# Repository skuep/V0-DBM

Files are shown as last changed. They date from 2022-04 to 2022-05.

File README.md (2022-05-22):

# V0-DBM
This is a high-resolution *differential pulley system* belt mod for the Z-axis on Voron 0 with optional Kirigami Bed support. There are quite a lot of belt mods out there, but this one differs significantly in how the mechanical advantage is implemented to achieve the same (or better) gearing ratio (notice the lack of an 80T pulley).

NOTE: This is an alpha version and heavy work in progress! Things are mostly tested and working, however there WILL be road bumps ahead and a Voron-style instruction manual is not available. Use the interactive 3D Model on Onshape below for assembly help. Please read this README carefully and in its entirety.

[See at Onshape](https://cad.onshape.com/documents/652155fb16d5bfa4e40363ce/w/0de7fce5d378ec45beba7939/e/0d8c25df57177126b288434d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) | [Demonstration Video](https://www.reddit.com/r/VORONDesign/comments/txs1nn/what_do_you_guys_think_of_a_differential_pulley/?sort=new)

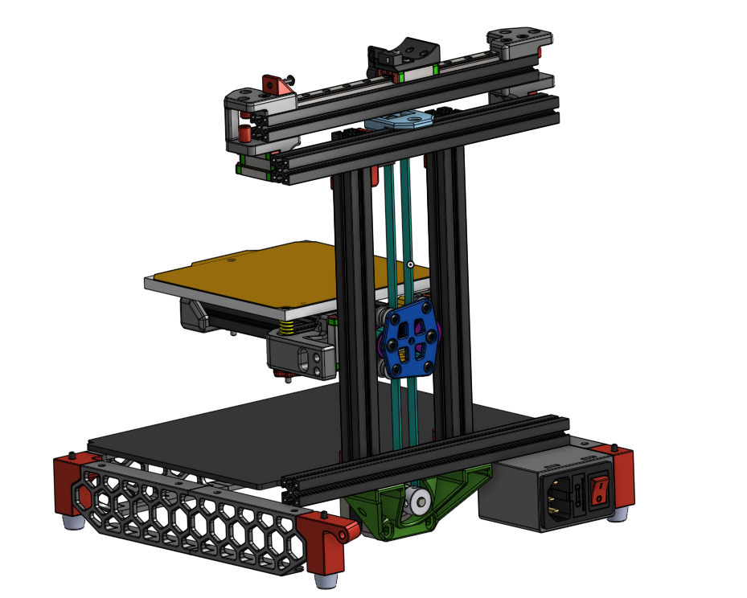
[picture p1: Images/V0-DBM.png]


## What?
A differential pulley system! It is a long known pulley system for achieving extremely high mechanical advantage using just pulleys and a belt.
See the [Wikpedia](https://en.wikipedia.org/wiki/Differential_pulley) article for more information on how this pulley system works. In this case, I split up the central shaft (connecting the two unequal pulleys) into two shafts and connected them with a small belt. This way we eliminate the belt crossing.

## Why?
I wanted a V0 Belt mod, that eliminates the 80T pulley for stepping down the motion and increasing torque that is used in all other belt mods. Also achieving relatively high mechanical advantage is no problem for differential pulley systems. In the differential pulley system, the "gear ratio" is integrated in the belt system. In this case, the two double pulleys have a combined teeth ratio of 27/33. Taking the Wikipedia article as a base, the following formula was derived to calculate the mechanical advantage in this system:

MA = 2/(1-r/R)-1 = 2/(1-27/33)-1 = 10

With the 20T motor pulley (2mm pitch, i.e. 40mm per revolution), this achieves a 40mm/10=4mm per revolution Z-axis advance or 0.01mm per stepper half-step with a regular 1.8° stepper motor.

Also the mechanism looks cool and is underrated. When you press me hard to find an advantage of this mod, I think this mod has less (special) parts than other belt mods.

NOTE: Theoretically gear ratios of 16 or 32 are possible with combined pulley ratios of 30/34 or 31/33, respectively. With a 16T pulley this allows a resolution of 2mm or even 1mm per revolution.

## Note on Kirigami Bed
For the Kirigami bed, you need to drill two extra 3mm holes for the two screws acting as the two shafts. Print and mount the drill-guide from the STLs to your Kirigami bed and drill in the designated holes with a 3mm drill bit. If your bed is made from Aluminium, you can deburr the drill-exit wound with a sharp exacto-knife.

## BOM
You need the following extra parts (this list is probably incomplete):
- 20T pulley for stepper motor
- 20T toothed idler (with bearing ID 3mm)
- 2x M3x40 BHCS (M3x30 BHCS with Kirigami Bed)
- 5x M3x16 BHCS
- 3x M3x6 BHCS
- 4x M3x8 BHCS
- 22x 0.5mm shim washer
- A bunch of heat-stake inserts
- 2GT belt 112mm (110mm also possible when changing to 27/26 and 26/33 pulleys, contact me in this case)
- 2GT belt 500mm

## ToDo
This repository is highly work in progress, the following things are still not satisfying:
- The endstop is actuated by the flange of one of the F623 bearings. Not nice but works for now.
- Documentation/Images on how to assemble

Feel free to use, open issues or leave alone :-)

## Known Issues
Unfortunately I could not get a very linear motion out of this system yet. I recorded Z movement with a dial test indicator in 0.1mm increments and the accuracy is only around +/-50 um (worst case). I think this is not enough and is probably due to the belt, that "pulls" the bed up being fed through multiple (3d printed) pulleys. In fact, both small pulleys and the belt-length can be found as a periodicity in the Z position error (even with original Gates belts). That is why I currently do not recommend this mechanism for the Z-axis drive.

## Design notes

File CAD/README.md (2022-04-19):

# Please download most current CAD data from the Onshape project

https://cad.onshape.com/documents/652155fb16d5bfa4e40363ce/w/0de7fce5d378ec45beba7939/e/0d8c25df57177126b288434d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

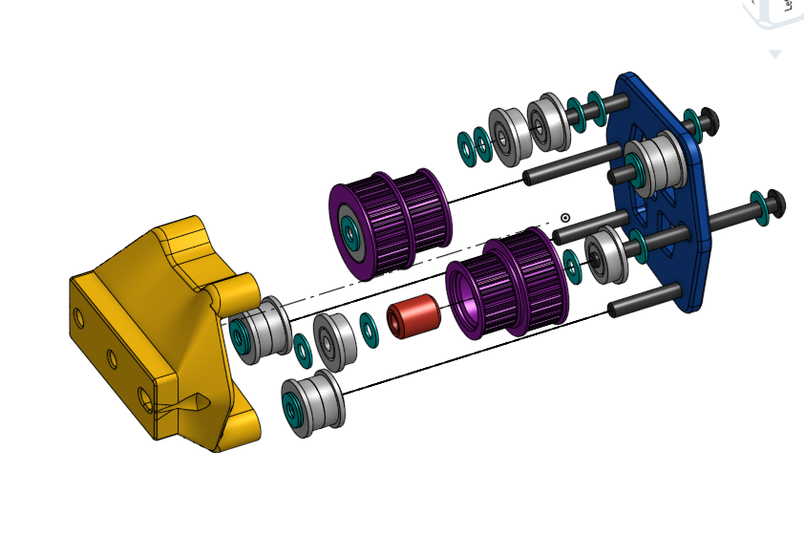
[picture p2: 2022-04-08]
Images/pulley-exploded.png

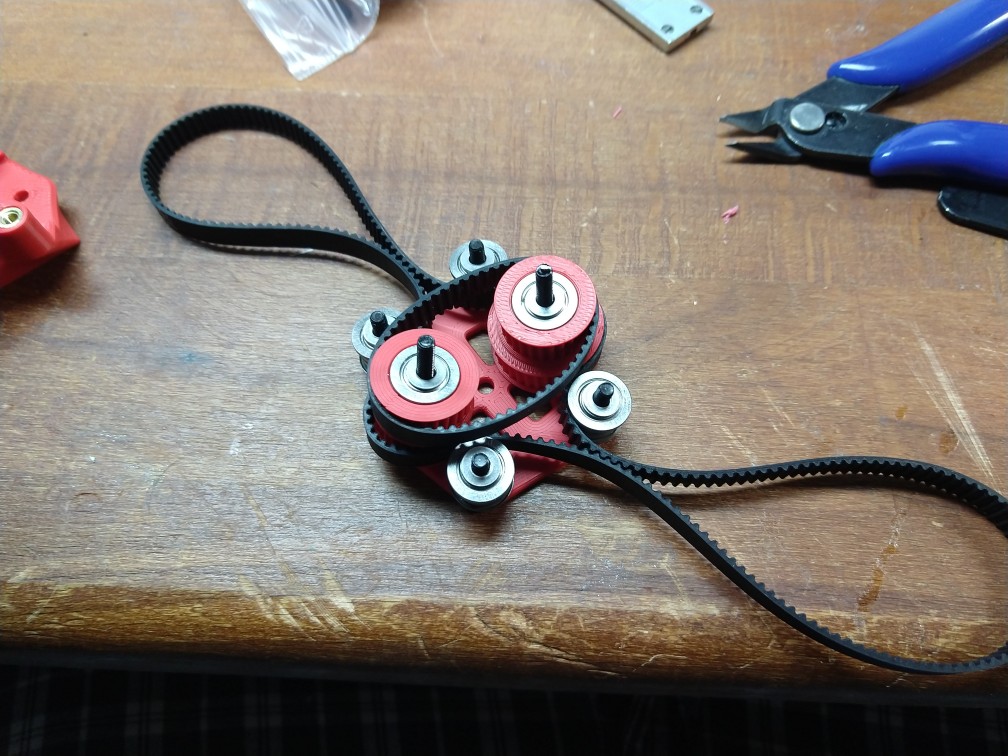
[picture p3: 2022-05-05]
Photos/Pulley-Assy.jpg

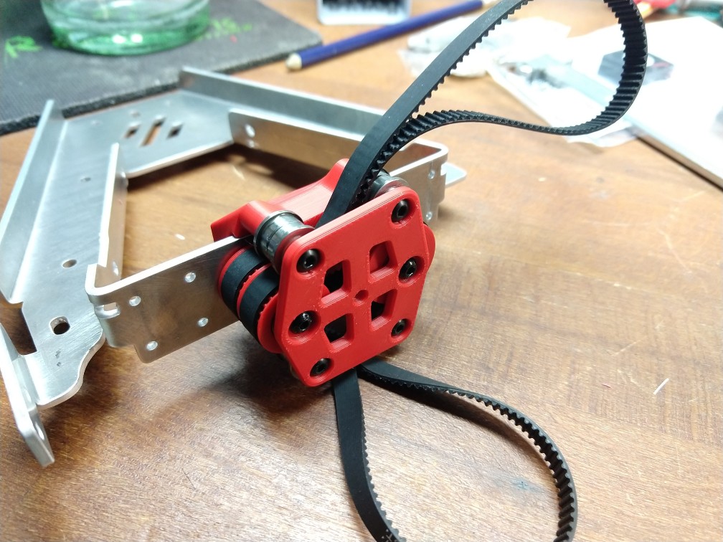
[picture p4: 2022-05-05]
Photos/Bedmount-Kirigami.jpg

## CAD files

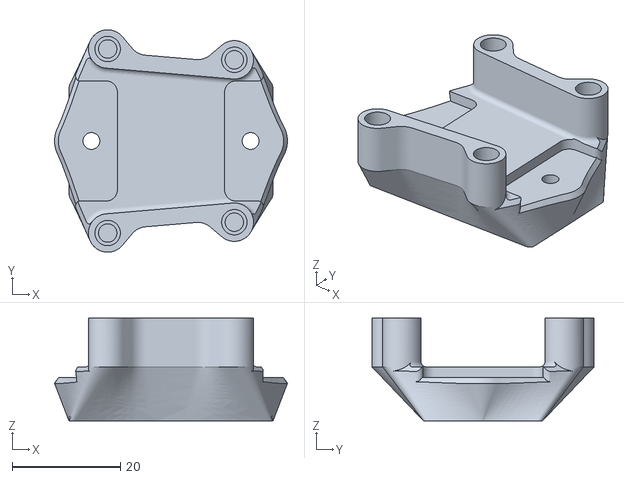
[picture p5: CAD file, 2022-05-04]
STL/Bedmount-Kirigami.stl
43.0 x 41.1 x 19.0

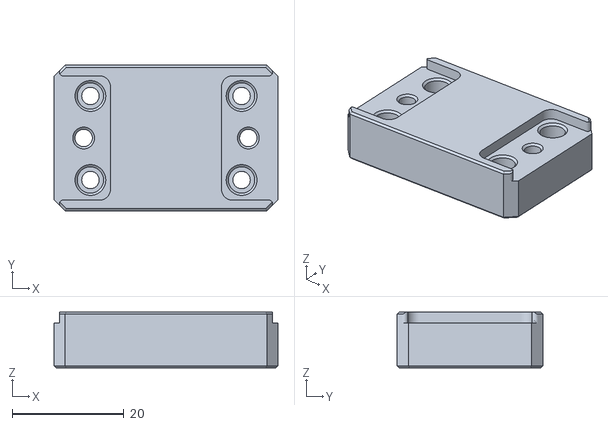
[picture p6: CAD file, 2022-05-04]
STL/Kirigami-Drillguide.stl
40.0 x 26.0 x 10.0

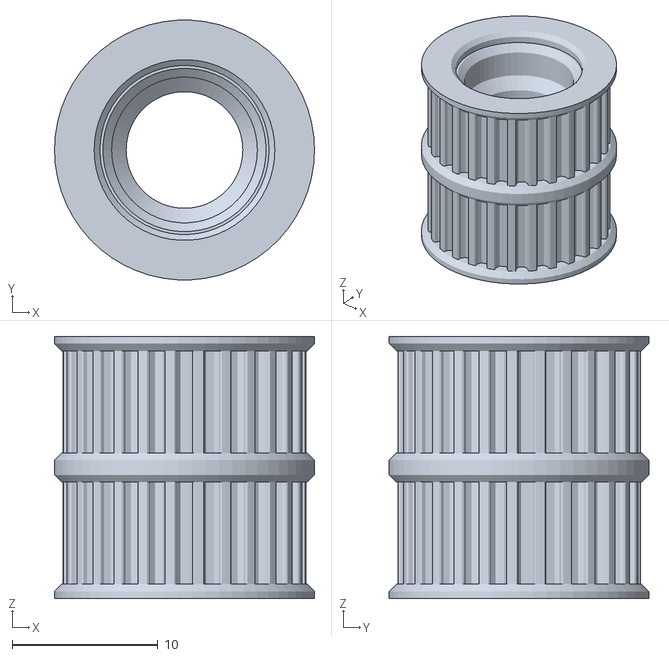
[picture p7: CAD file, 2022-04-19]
STL/Double-Pulley-27-27.stl
17.8 x 17.8 x 18.0

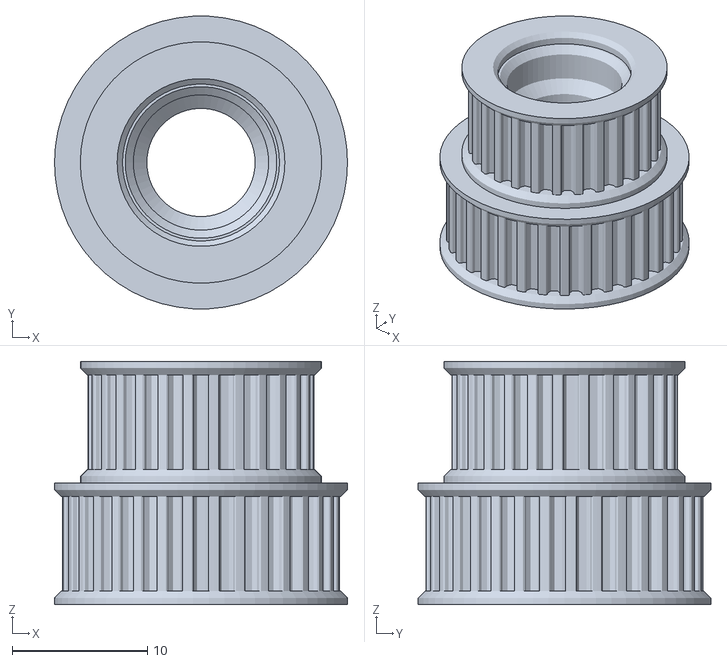
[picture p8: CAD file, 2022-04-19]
STL/Double-Pulley-27-33.stl
21.7 x 21.6 x 18.0

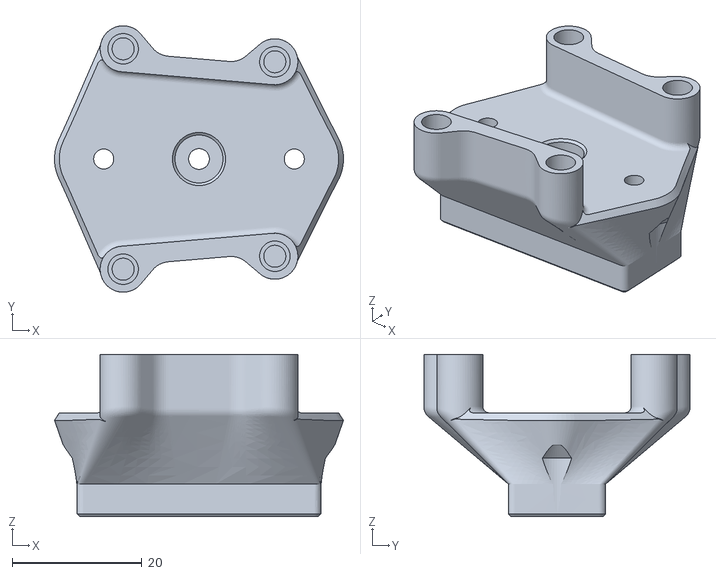
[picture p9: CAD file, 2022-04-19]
STL/Bedmount-Standard.stl
44.6 x 41.1 x 25.0

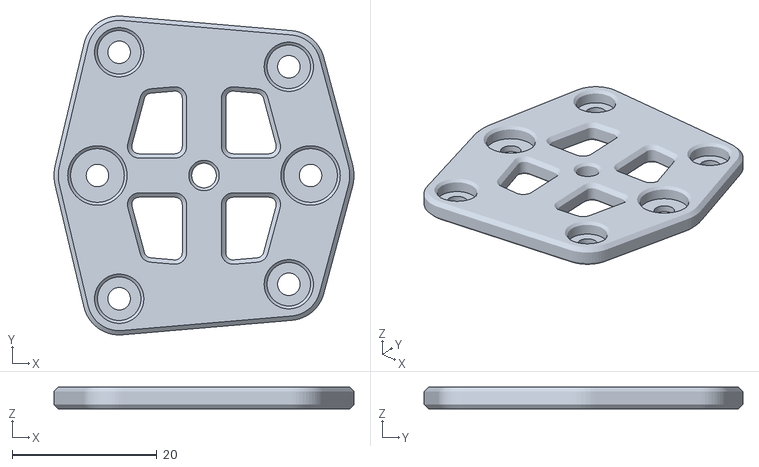
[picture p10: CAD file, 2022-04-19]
STL/Brace.stl
41.4 x 44.0 x 3.00

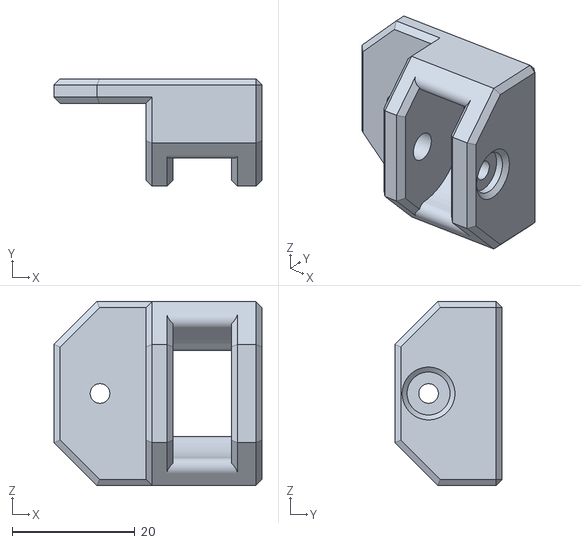
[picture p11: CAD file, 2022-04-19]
STL/Idler-Bracket.stl
33.9 x 17.5 x 30.0

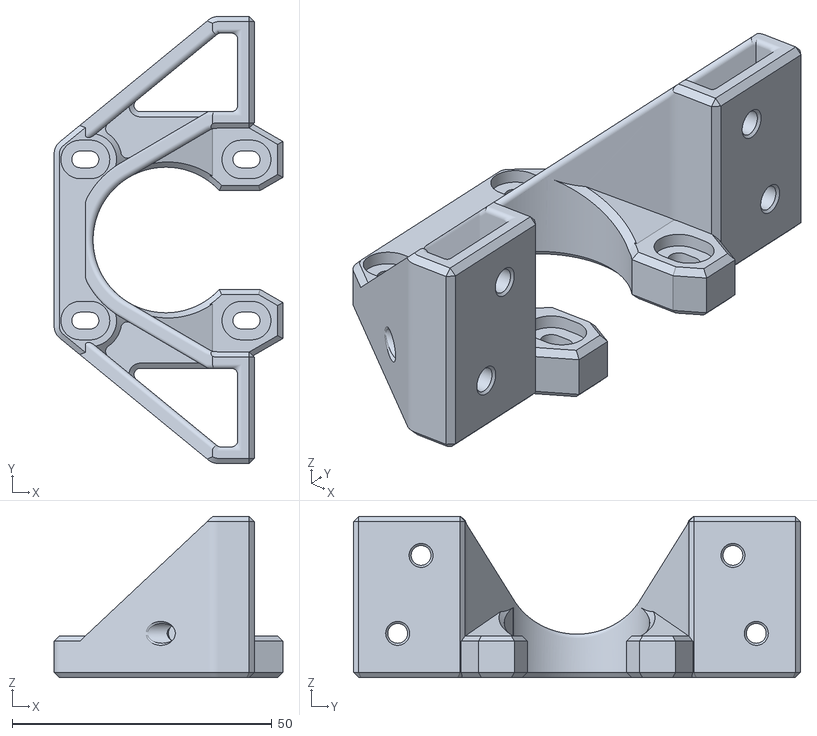
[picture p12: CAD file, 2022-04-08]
STL/Motor-Mount.stl
44.0 x 86.0 x 31.0

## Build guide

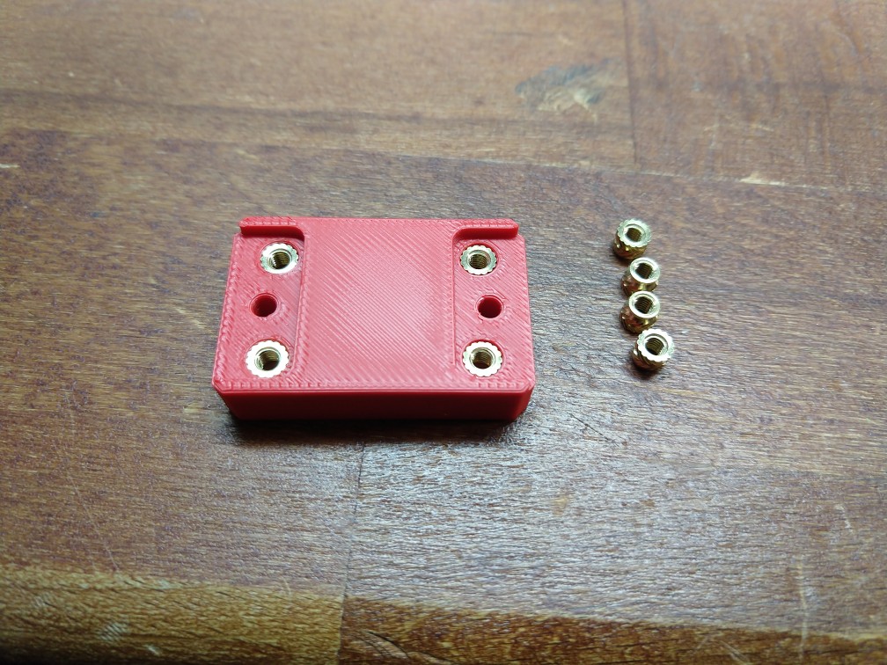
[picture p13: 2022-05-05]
Photos/Kirigami-Drillguide-1.jpg

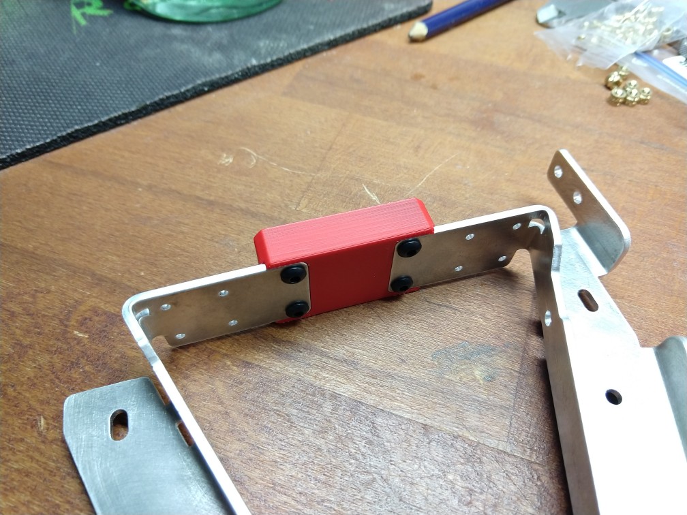
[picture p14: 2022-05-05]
Photos/Kirigami-Drillguide-2.jpg

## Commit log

2022-04-08 Added script for calculating ratio of mechanical advantage for double-serial-double-pulley differential belt
2022-04-08 Added CAD model
2022-04-08 Added STL files for 3D printed parts
    [Brace.stl, Double-Pulley-A.stl, Double-Pulley-B.stl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]
2022-04-09 Adjusted hole spacing of the two double-pulleys. The plan is to omit any adjustment mechanism entirely. Lets see how this works out.
    [Brace.stl]
2022-04-09 Simplified idler bracket
    [Idler-Bracket.stl]
2022-04-18 Improved belt ratio calculation script to remove duplicates (among other things)
2022-04-18 Fixed wrong position of toothed idler
    [Idler-Bracket.stl]
2022-04-18 Made bearing seat a press-fit
    [Double-Pulley-A.stl, Double-Pulley-B.stl]
2022-04-19 Added hint to Onshape project for most current CAD data
2022-04-19 Fixed unverified and wrong formula for mechanical advantage. Changed pulleys for overall mechanical advantage using new formula to 10 Updated all relevant parts due to pulley change
    [Brace.stl, Double-Pulley-27-27.stl, Double-Pulley-27-33.stl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]
2022-04-20 Added STLs for Kirigami bed support
    [Bedmount-Kirigami.stl, Bedmount-Standard.stl, Kirigami-Drillguide.stl]
2022-04-20 Updated CAD model snapshot
2022-04-20 Adjusted hole for threaded insert
    [Bedmount-Kirigami.stl]
2022-04-22 Update README.md
    Added note regarding optional 110mm belt length instead of 112mm
2022-05-04 Improved Kirigami drill guide and changed hole size to 3mm
    [Kirigami-Drillguide.stl]
2022-05-04 Improved fit on Kirigami bed
    [Bedmount-Kirigami.stl]
2022-05-05 Update README.md
    Updated BOM
2022-05-05 Update README.md
    Updated ToDo list. Will leave the current solutions for 3d parts, since they work quite well for now.
2022-05-05 Update README.md
    Added note for Kirigami bed
2022-05-05 Added additional gear ratios that are calculated
2022-05-05 Update README.md
    Added a note about additional possible gear ratios
